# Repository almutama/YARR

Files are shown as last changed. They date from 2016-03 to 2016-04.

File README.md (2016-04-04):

#YARR (Yet Another RepRap)

YARR is an open source 3D printer designed and developed by LEDs & Chips Creative Electronics in Lisbon, Portugal. YARR is based on the [CoreXY](http://corexy.com/) technique and adds several improvements to other printers.  YARR is available either as a made to order kit or fully assembled from [Leds & Chips](www.ledsandchips.com)

##Technical specifications

###Dimensions
Custom-Sized
Built Version 7575
- Printer Dimensions: 1250(X) x 1250(Y) x 1250 mm(Z without bowden tupe support)
- Print Area Dimensions: 750(X) x 750(Y) x 750 mm(Z)
Built Version 5050
- Printer Dimensions: 1000(X) x 1000(Y) x 1000 mm(Z without bowden tupe support)
- Print Area Dimensions: 500(X) x 500(Y) x 500 mm(Z)

###Mechanical Construction
- OpenBuilds V-Slot aluminium frame
- OpenBuilds Wheels carriages X, Y, Z
- 4 motors Z Axis
- Flexible aluminium coupling for threaded rods of Z Axis
- 9 point print base levelling system with cushioning
- Quick change system for multi tools head
- Brushless Fans with axial ball bearings.

###Print resolution
- Very high: 60 microns
- High 100 microns
- Medium 200 microns
- Low 300 microns

###Extruder Mechanics
Custom extruder design
- 0.4mm nozzle
- Heat-sinks with axial fan
- Part cooling nozzle
Print speed
- Recommended speed: 70 mm / s
- Maximum recommended speed: 200 mm / s

###Electronics
- Any RepRap electronics conforming to RepRap Interface Standard RIS 1. Default: RAMPS 1.4
- LCD Panel with rotary encoder and push-button navigation for autonomous printing
- Cold glass base (size:750 x 750 x 4 mm)
- Power supply: 220 AC 12 DC 100W
- Thermistor 100k EPCOS
- Heating element: 12V 40W

###Software
- Firmware derivative Marlin
- Recommended environment: Cura Software
- Supported Files:. Gcode
- OS supported:
	- Windows XP and above
	- Mac OS X and above
	- Linux

###Communications
- Standard SD card reader
- USB Port Type B

###Materials
- PLA Filament 1.75-mm

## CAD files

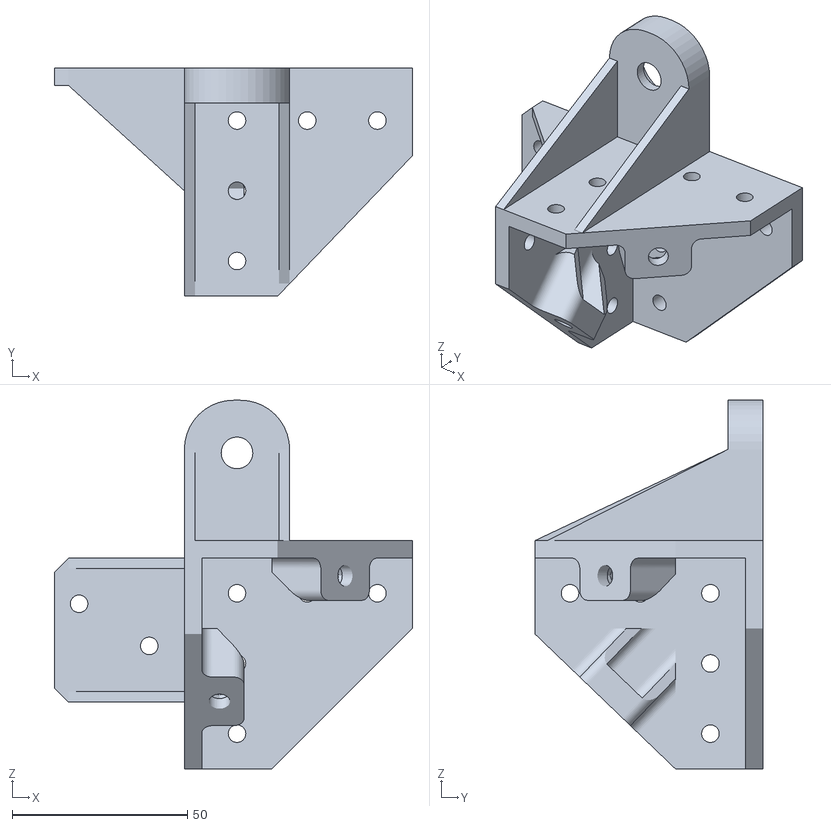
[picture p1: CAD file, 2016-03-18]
cad_models/STL/stl 01/roll support xy 02.STL
102.0 x 65.0 x 105.0

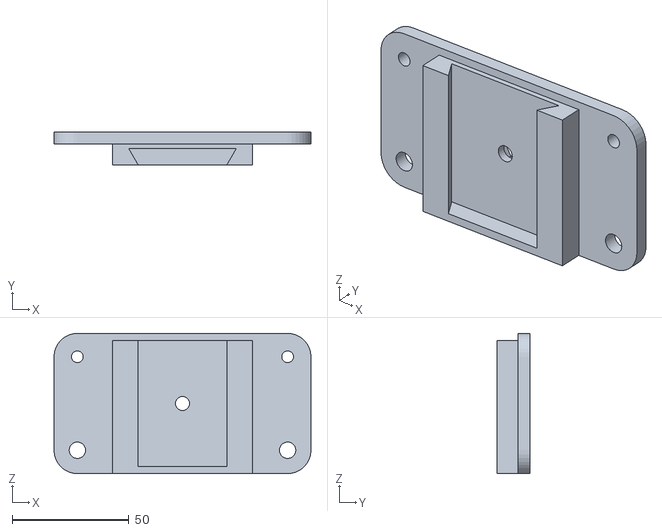
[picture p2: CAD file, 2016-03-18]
cad_models/STL/stl 02/slider plate y 02.STL
110.0 x 14.0 x 60.0

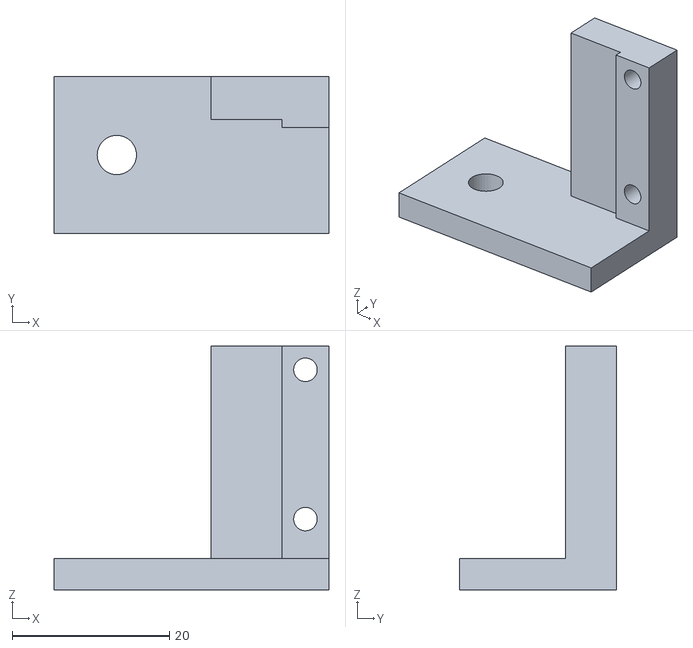
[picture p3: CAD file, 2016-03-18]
cad_models/STL/stl 03/endstop holder.STL
35.0 x 20.0 x 31.0

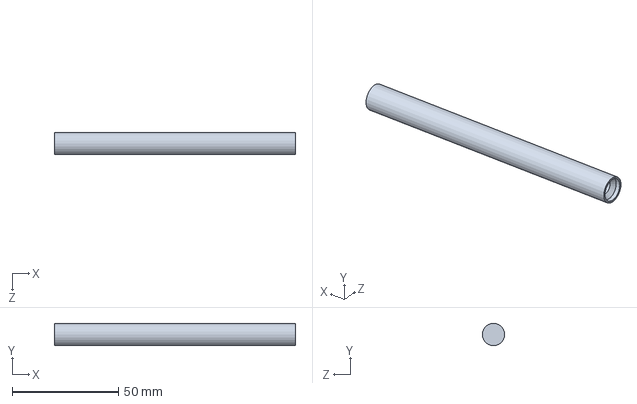
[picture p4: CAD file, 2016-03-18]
cad_models/STL/stl 04/knife body 01.SLDPRT
113.3 x 10.5 x 10.5 mm

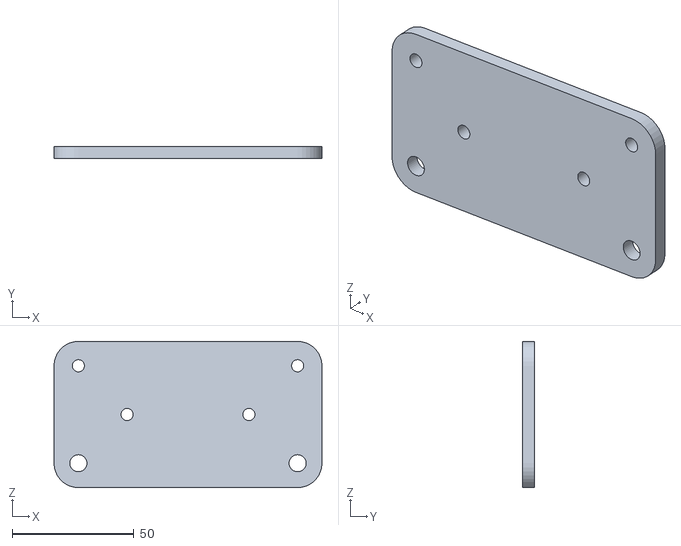
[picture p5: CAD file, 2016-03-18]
cad_models/STL/stl 05/slider plate y 01.STL
110.0 x 5.00 x 60.0

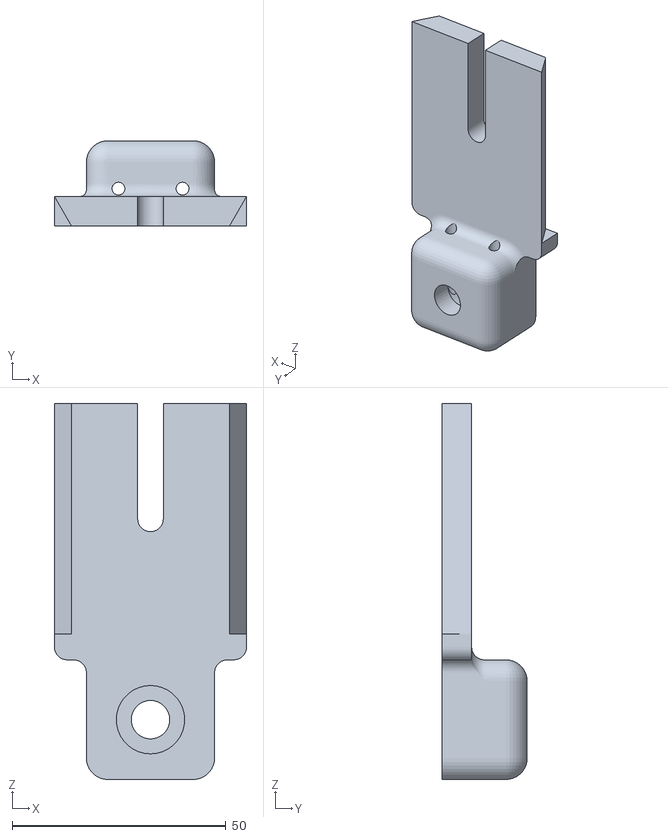
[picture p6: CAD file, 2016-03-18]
cad_models/STL/stl 06/extruder bowden 175 support 01.STL
45.0 x 20.0 x 88.0

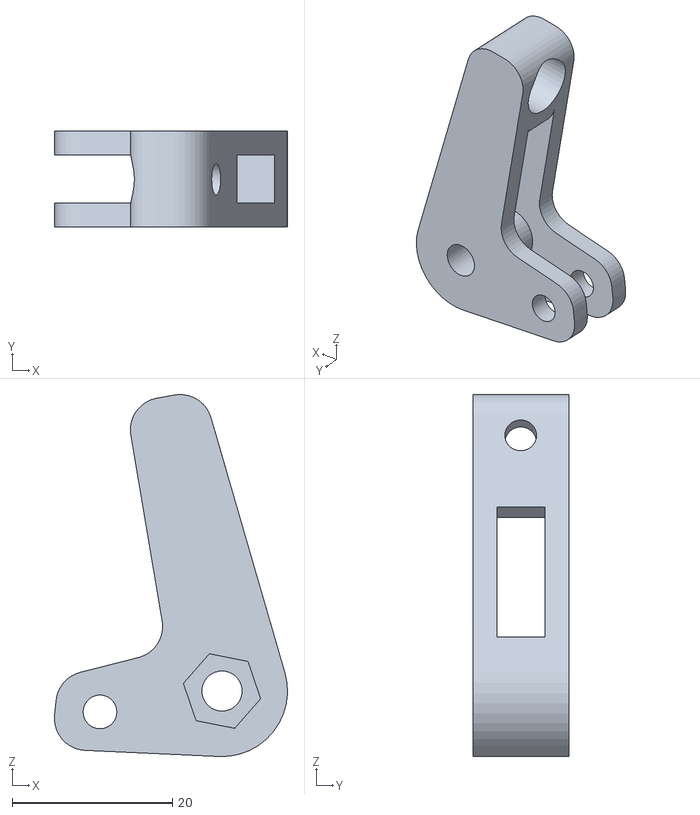
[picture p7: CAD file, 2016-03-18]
cad_models/STL/stl 07/extruder filament pusher 02.STL
29.0 x 12.0 x 45.1

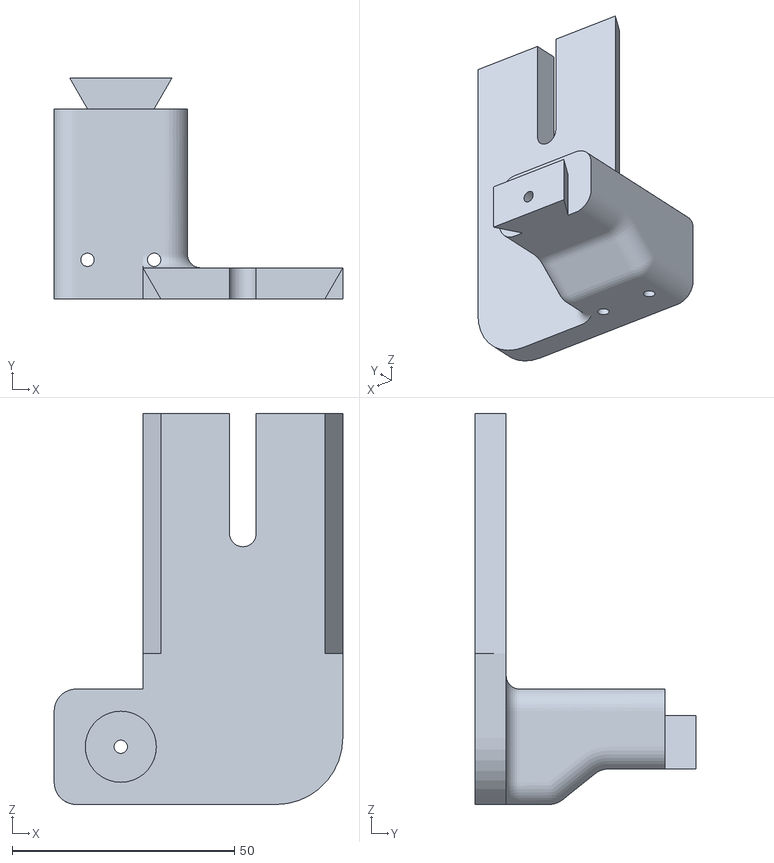
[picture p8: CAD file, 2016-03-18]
cad_models/STL/stl 08/extruder mini bowden support 01.STL
65.0 x 49.7 x 88.0

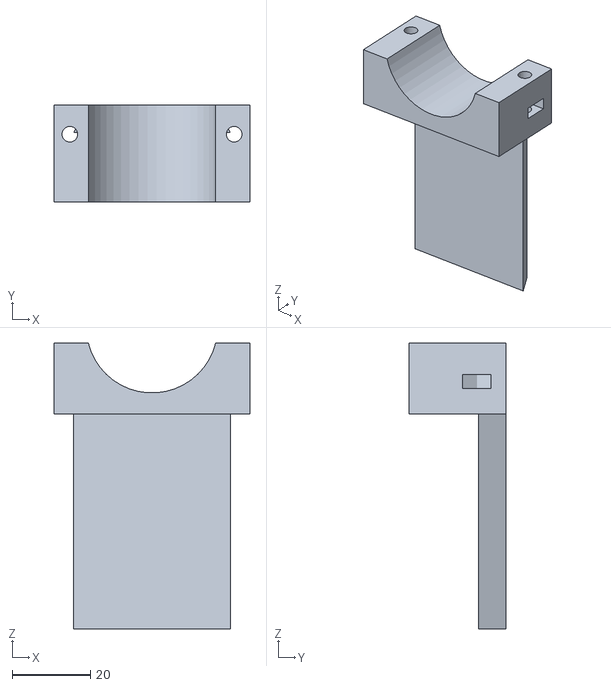
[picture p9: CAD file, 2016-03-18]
cad_models/STL/stl 09/mill adapter 01 01.STL
50.0 x 24.9 x 73.1

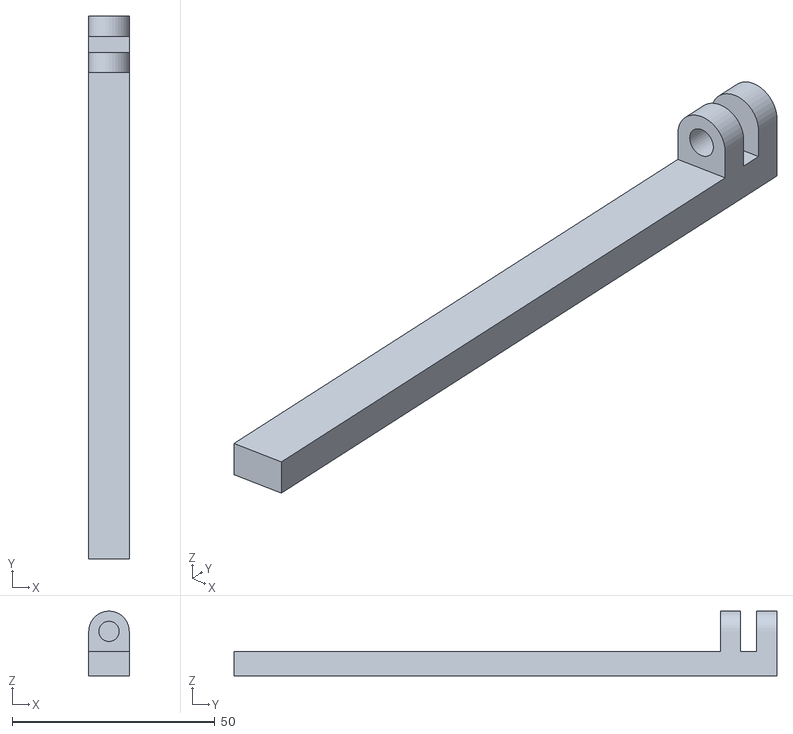
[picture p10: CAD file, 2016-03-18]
cad_models/STL/stl 10/endstop ruler 01.STL
10.00 x 134.0 x 16.0

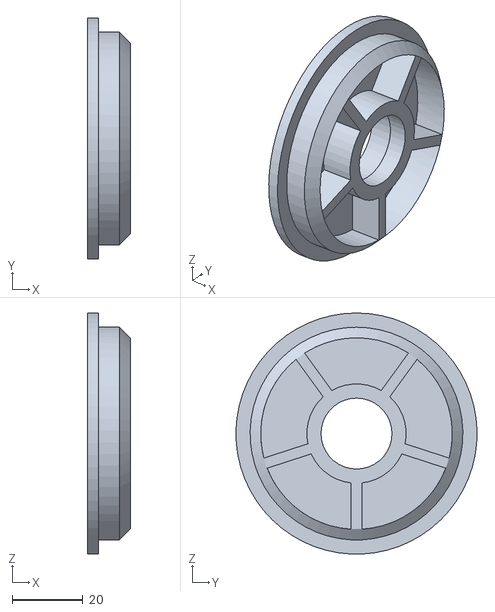
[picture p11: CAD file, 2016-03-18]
cad_models/STL/stl 11/spool holder bearing insert 04.STL
12.0 x 68.0 x 68.0

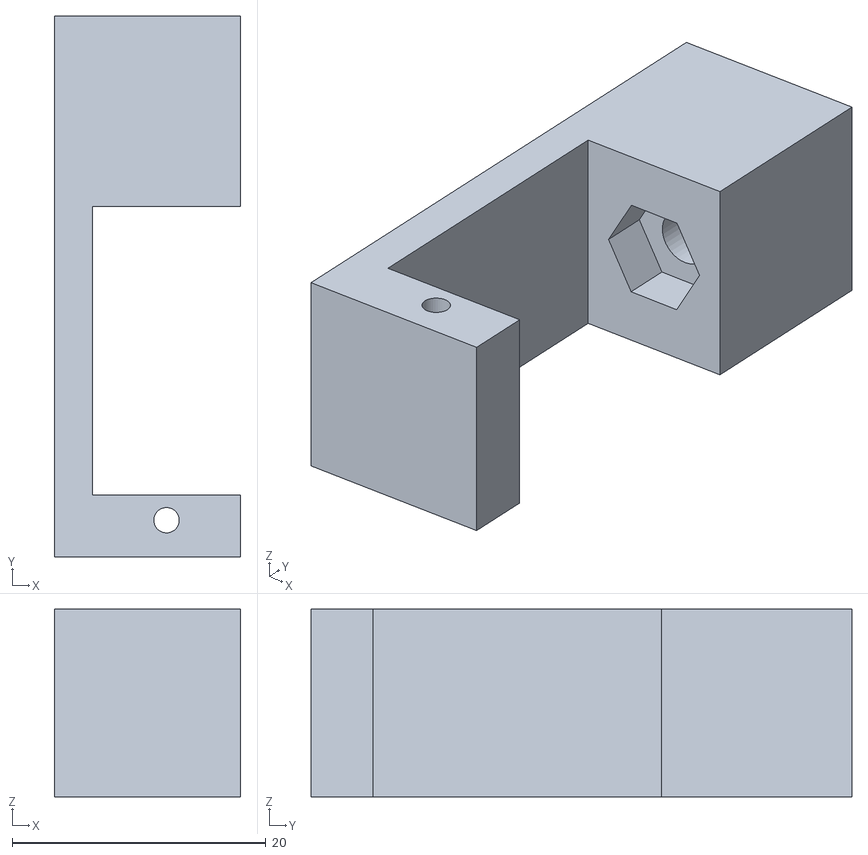
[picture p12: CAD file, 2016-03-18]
cad_models/STL/stl 12/suport servo.STL
14.7 x 42.6 x 14.8

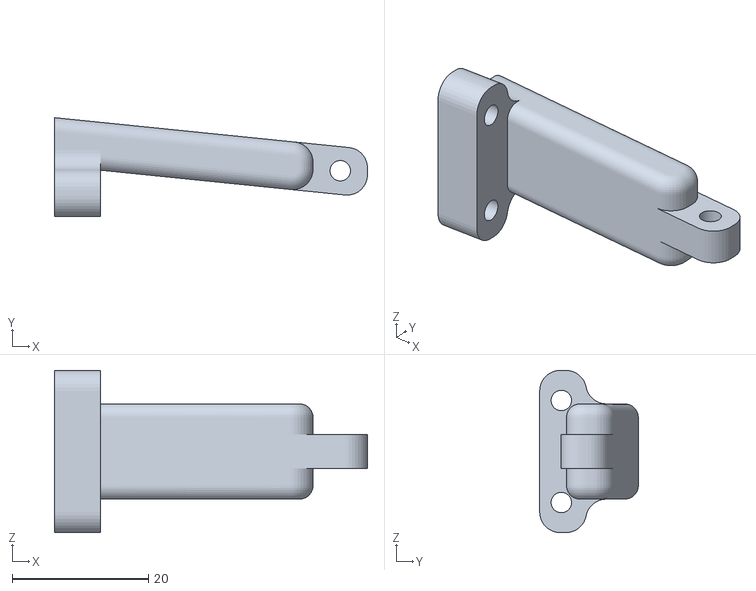
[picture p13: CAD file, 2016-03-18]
cad_models/STL/stl 13/fan support direct drive 01.STL
46.0 x 14.5 x 23.8

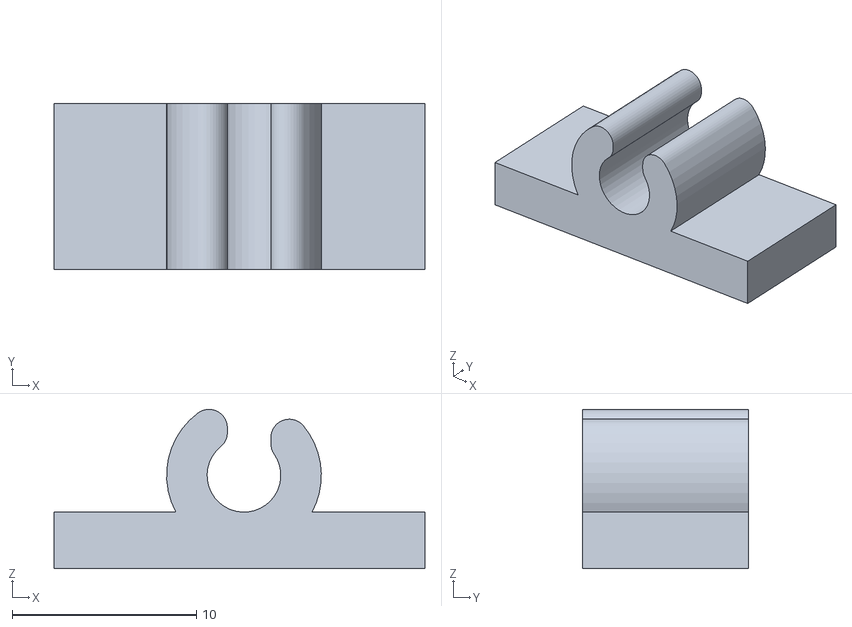
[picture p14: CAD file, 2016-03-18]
cad_models/STL/stl 14/dobradiça fémia.STL
20.1 x 9.00 x 8.64

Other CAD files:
cad_models/STL/stl 15/cutting adapter 02.STL
cad_models/STL/stl 16/slider x plate 01.STL
cad_models/STL/stl 01/slider plate z 02.STL
cad_models/STL/stl 02/slider x plate 01.STL
cad_models/STL/stl 01/roll support xy 01.STL
cad_models/STL/stl 03/cable hider 01.STL
cad_models/STL/stl 03/cable hider 02.STL
cad_models/STL/stl 03/cable hider 03.STL
cad_models/STL/stl 03/endstop holder 01.STL
cad_models/STL/stl 04/glass support angle.STL
cad_models/STL/stl 04/glass support handle.STL
cad_models/STL/stl 04/glass support straight.STL
cad_models/STL/stl 04/knife holder.STL
cad_models/STL/stl 05/slider plate x greg extruder.STL
cad_models/STL/stl 06/bolt hobber bearing.STL
cad_models/STL/stl 06/extruder filament pusher 02.STL
cad_models/STL/stl 07/extruder bearing adapter 01.STL
cad_models/STL/stl 07/extruder filament pusher 03.STL
cad_models/STL/stl 07/extruder motor support 01.STL
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

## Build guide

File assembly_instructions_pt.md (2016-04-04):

##Passo 1
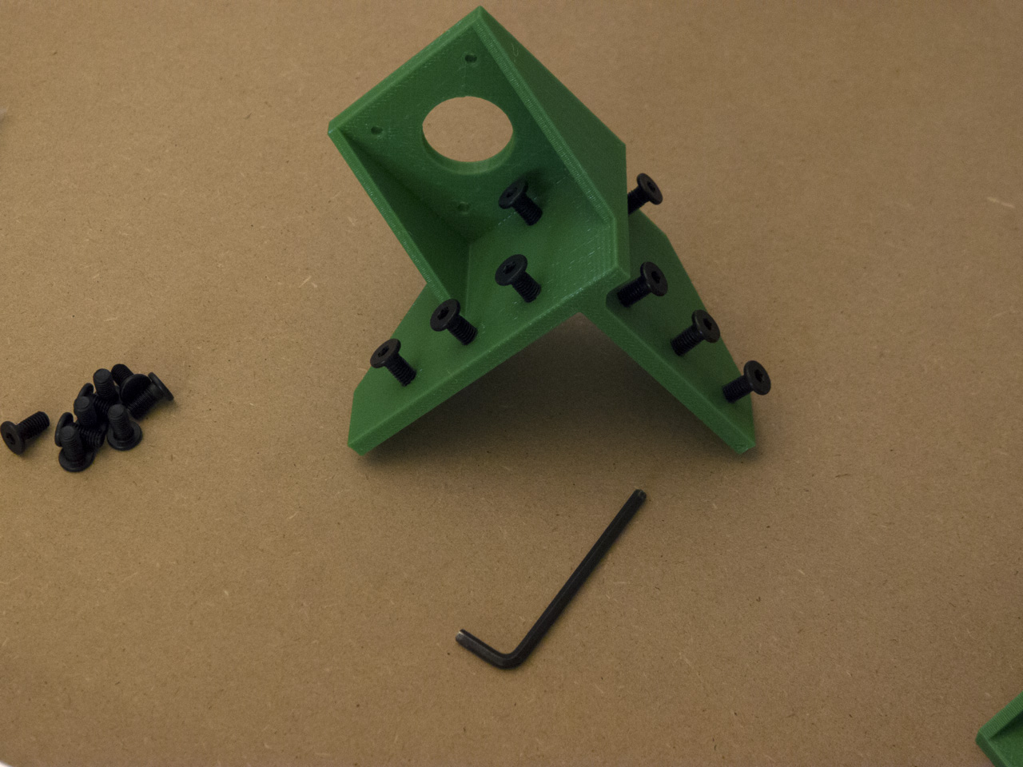
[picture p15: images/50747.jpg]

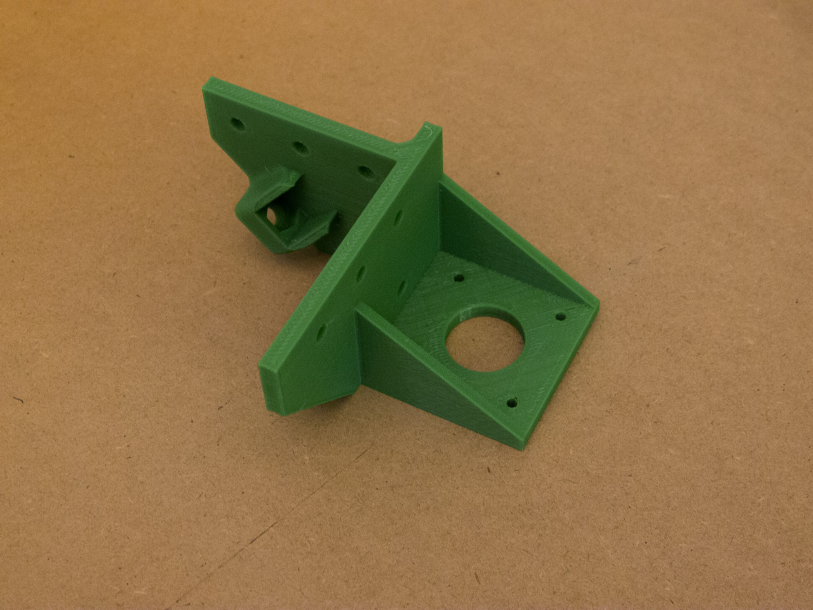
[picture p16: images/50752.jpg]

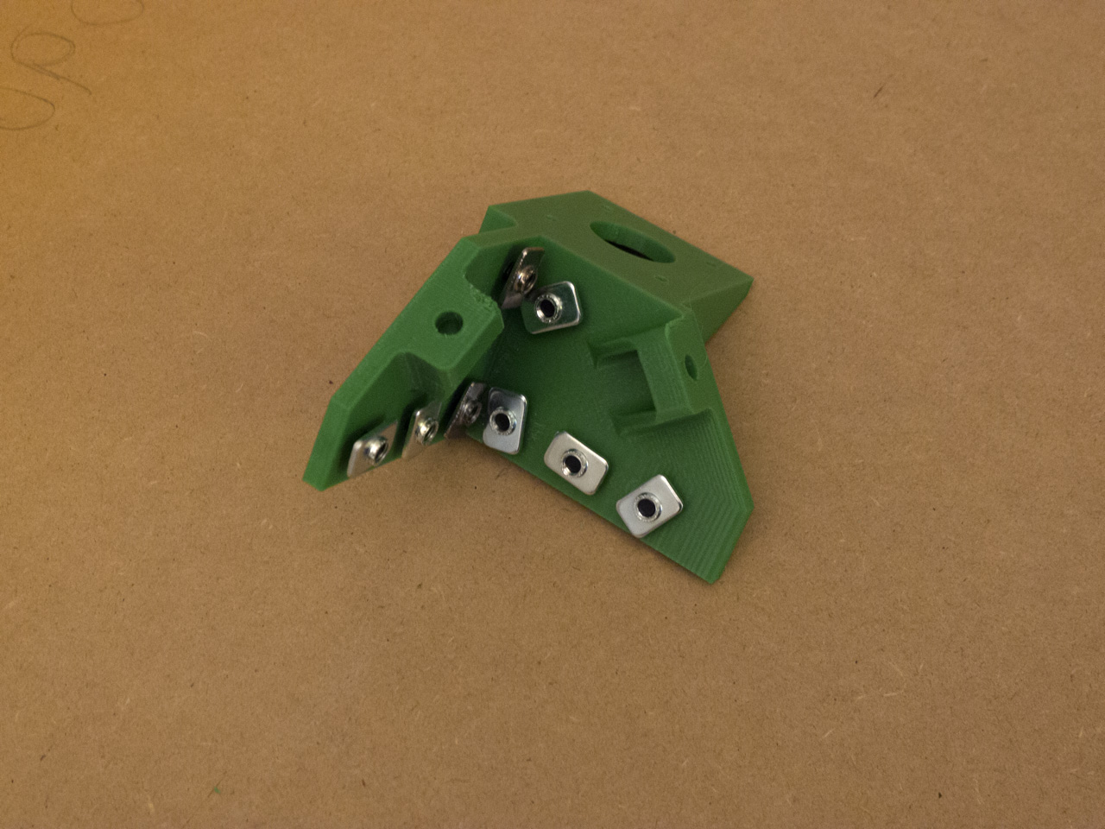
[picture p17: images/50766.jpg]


Coloque 8 parafusos M5-10mm como descrito na figura bem como as respectivos Tee Nuts.
Repita este procedimento para as outras 3 peças.  

##Passo 2
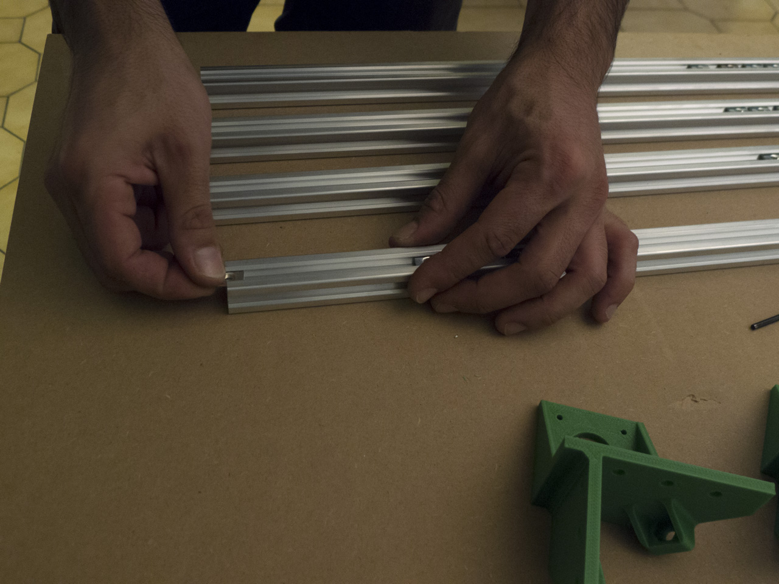
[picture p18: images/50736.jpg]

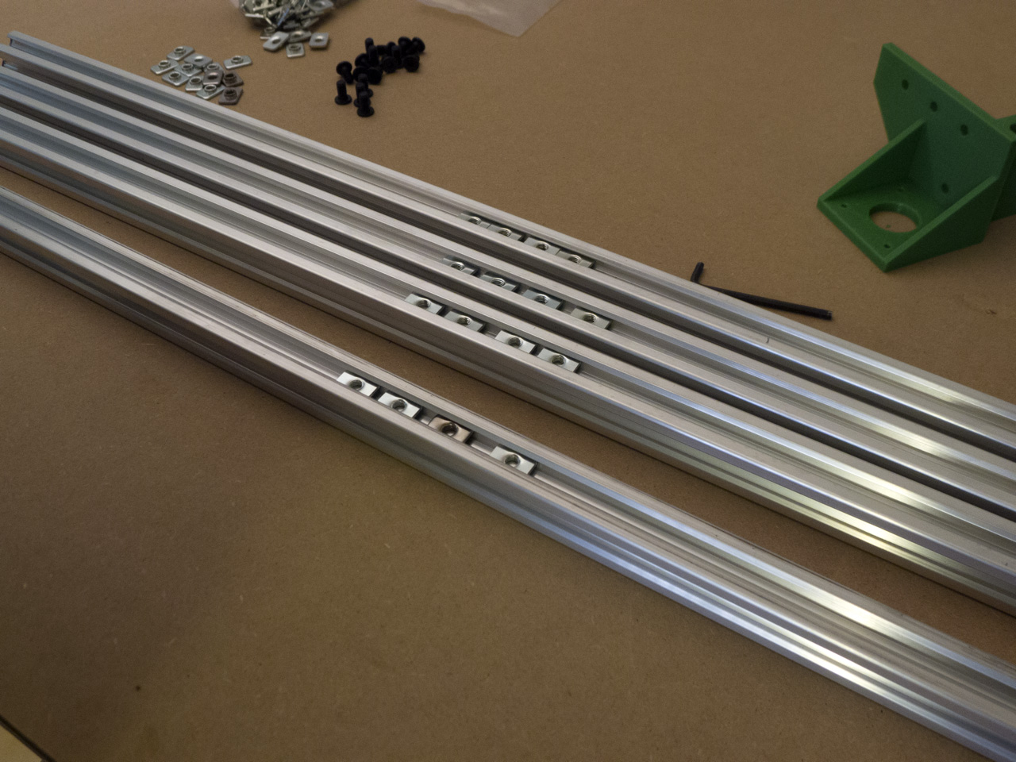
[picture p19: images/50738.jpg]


Introduza 4 tee nuts num perfil de aluminium, tenha em atenção pois a parte saliente de cada Tee nut tem que ficar para o lado de dentro do perfil.
Repita este procedimento mais 3 vezes.
Este 4 perfis farão a base da máquina e estes 4 Tee Nuts, por varão vão servir para fixar a impressora á plataforma de madeira, que servirá de base.
 
##Passo 3
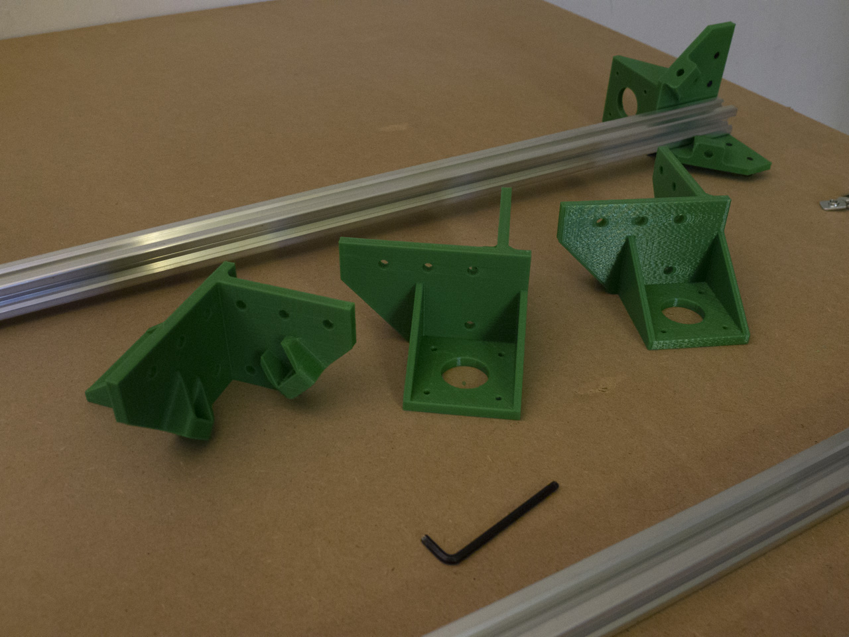
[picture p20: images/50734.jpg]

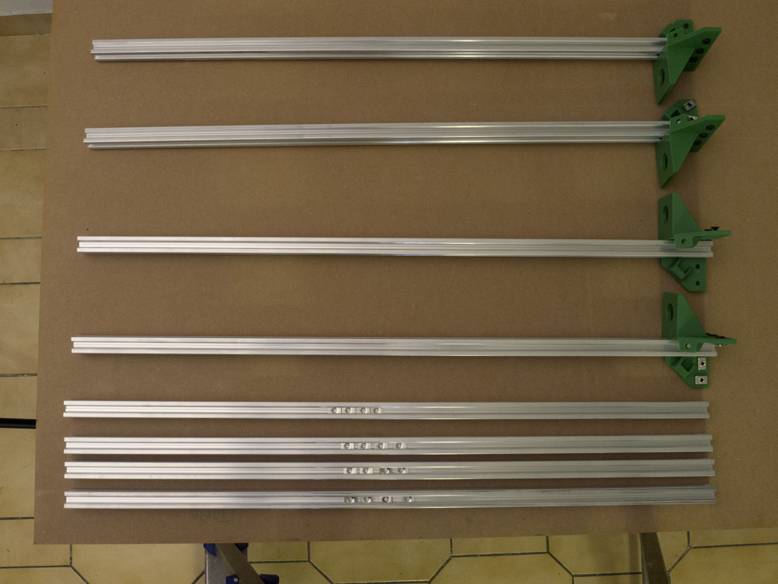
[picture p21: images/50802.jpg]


Encaixe um perfil de aluminium ao alto, em cada peça previamente preparada no passo 1, tal como se apresenta na figura ao lado.

##Passo 4
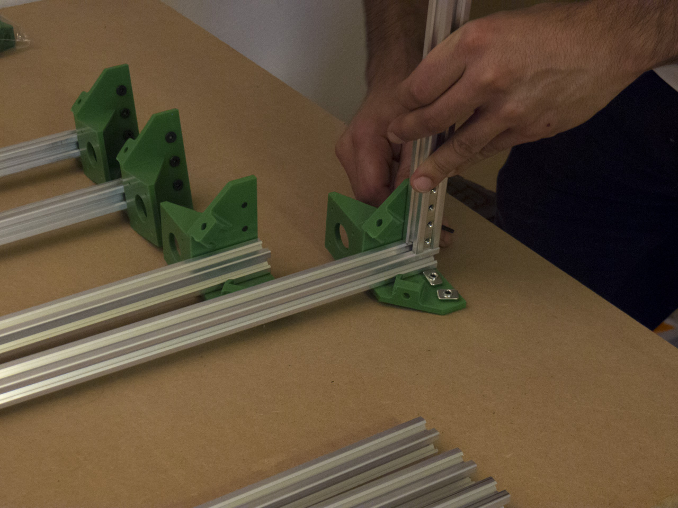
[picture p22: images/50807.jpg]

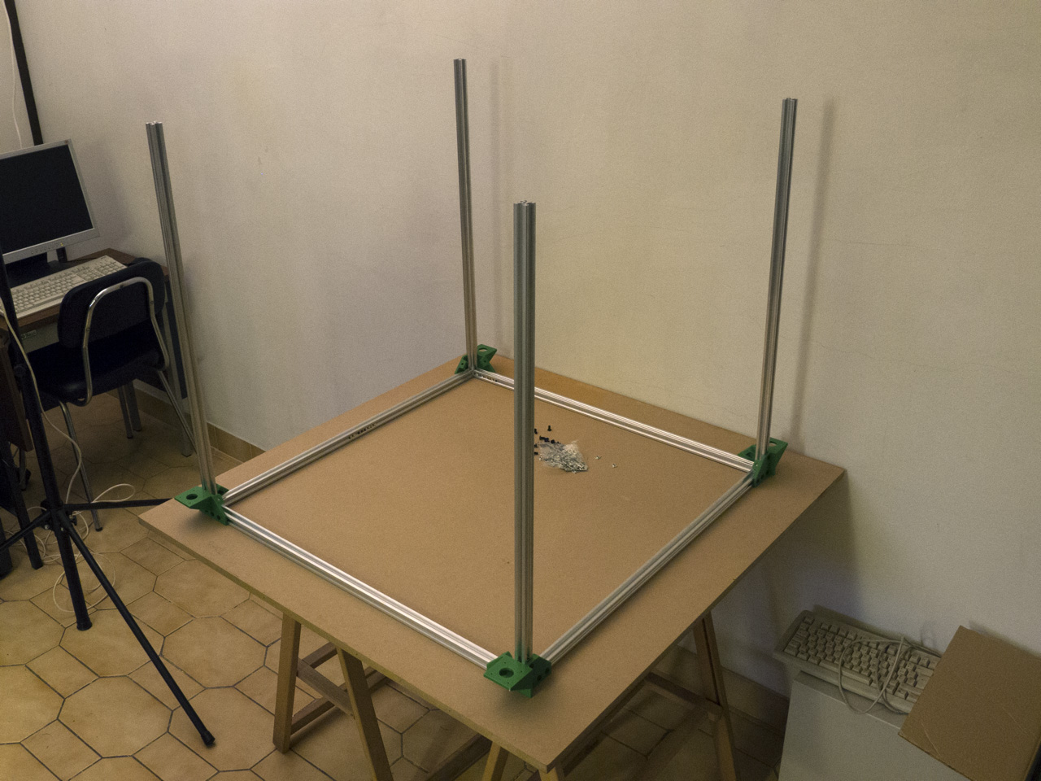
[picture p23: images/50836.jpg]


Coloque os varões, previamente preparados no passo 2, assegurando que os 4Tee nuts ficam virados para o lado de dentro da máquina.
É importante que a peças impressas fiquem com a disposição como se apresentam na figura.

##Passo 5
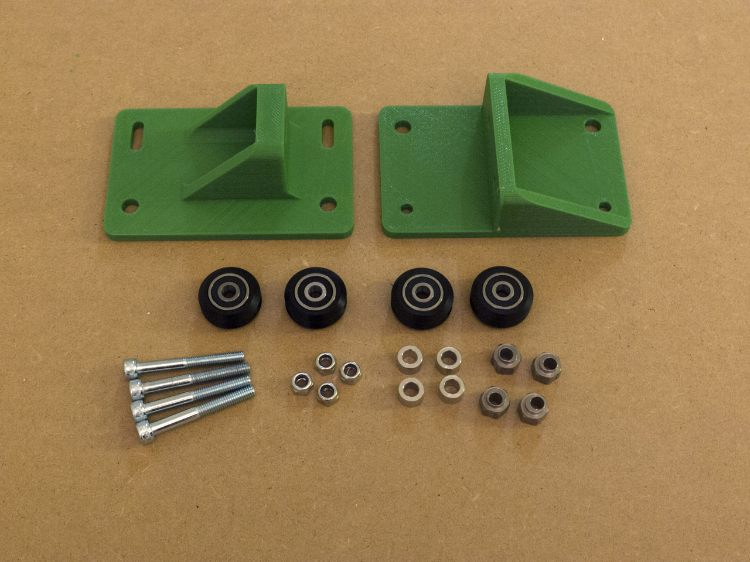
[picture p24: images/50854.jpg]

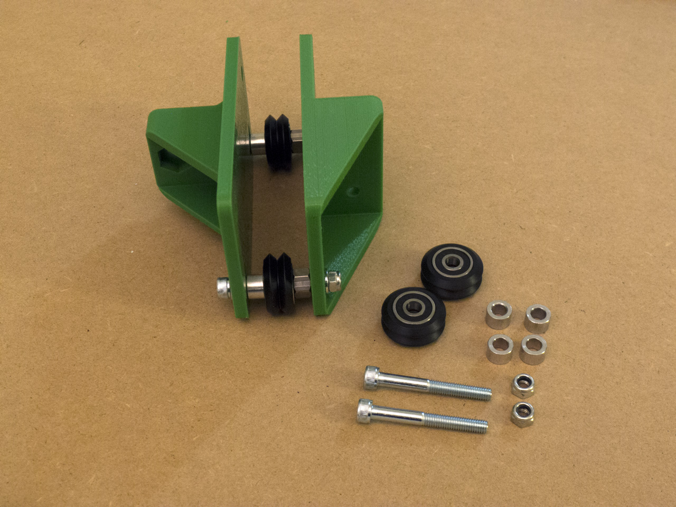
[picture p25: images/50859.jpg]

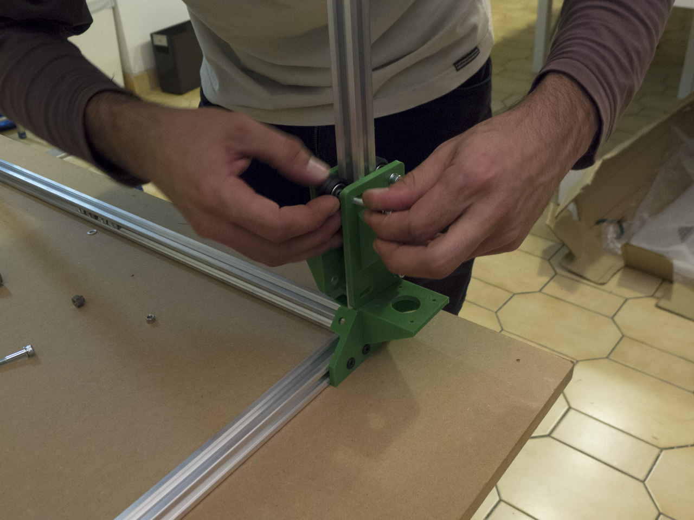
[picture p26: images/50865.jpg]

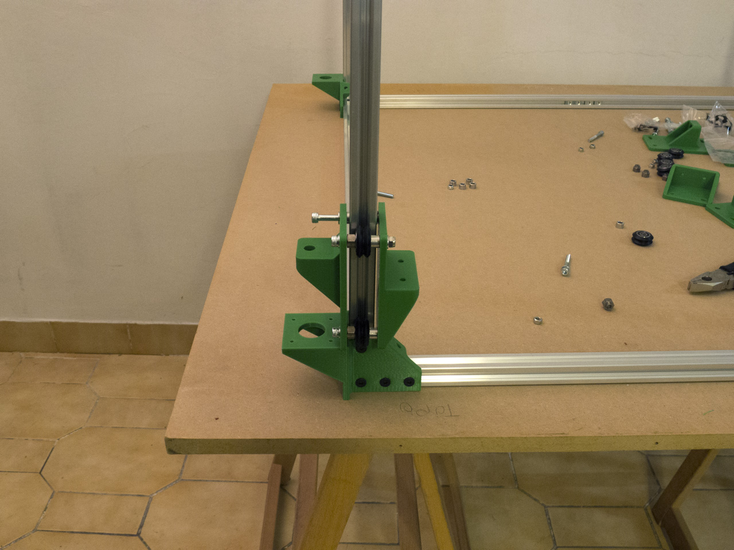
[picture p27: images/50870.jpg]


Efetue a montagem do carril do eixo Z como descrita na imagem.
repita este passo 3 vezes.
Introduza um carril em cada perfis que se encontra na vertical.
Tenha em atenção que os espaçadores excêntricos tem que está rodados de forma a que as rodas não façam força no perfil de aluminium.  
Após a sua instalação a tensão nas rodas deve ser ajustada
rodando os excêntricos até sentir que as rodas ficam á justa e não rodam só por si. 

##Passo 6
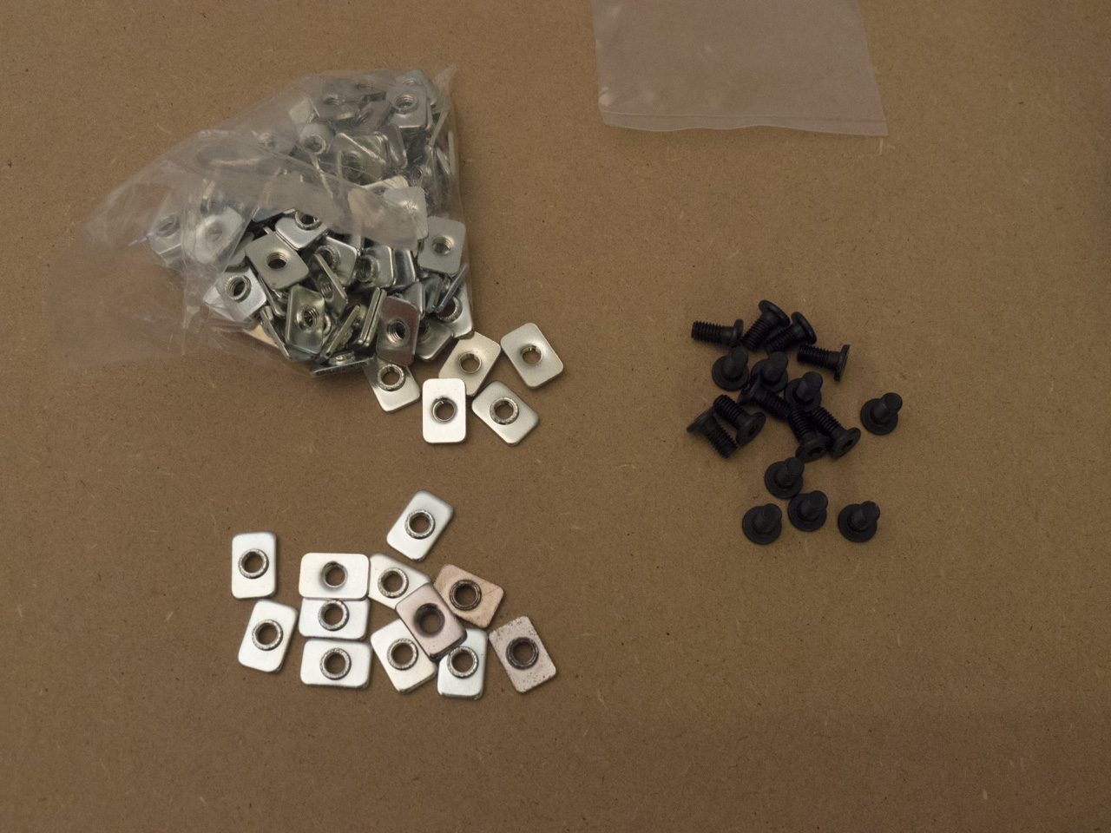
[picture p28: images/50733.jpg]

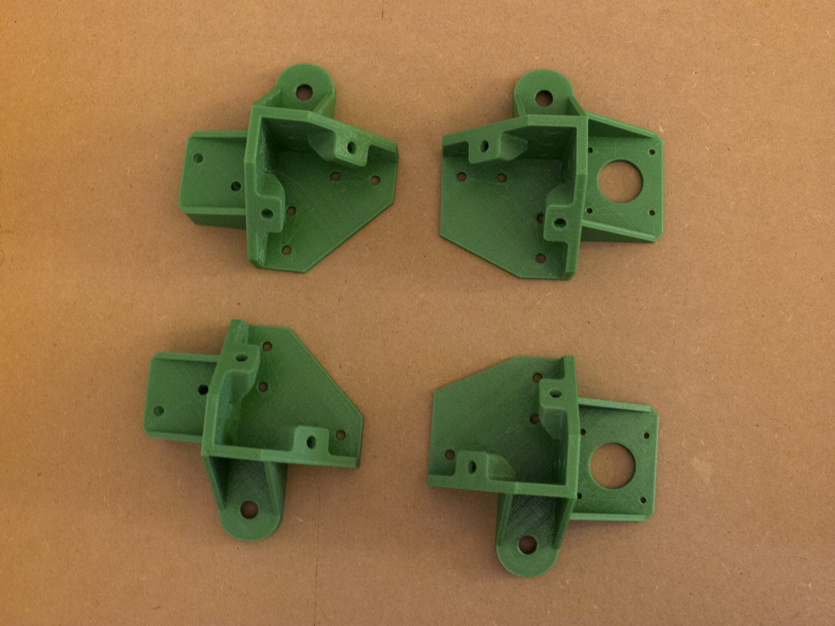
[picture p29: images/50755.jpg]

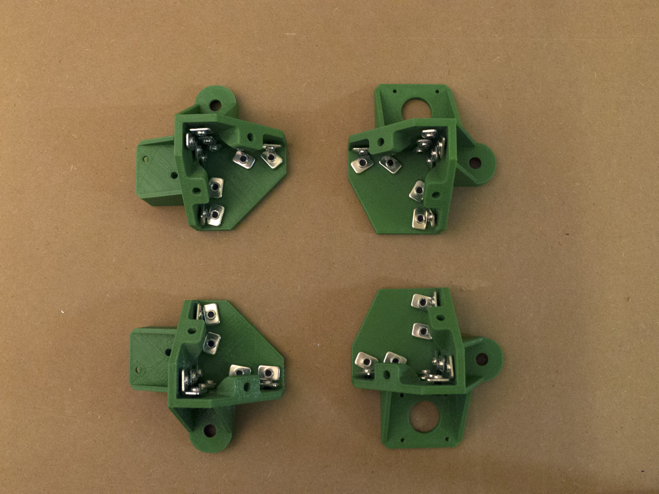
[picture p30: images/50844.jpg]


Coloque 8 parafusos M5-10mm como descrito na figura bem como as respectivos Tee Nuts.
Repita este procedimento para as outras 3 peças.  

##Passo 7
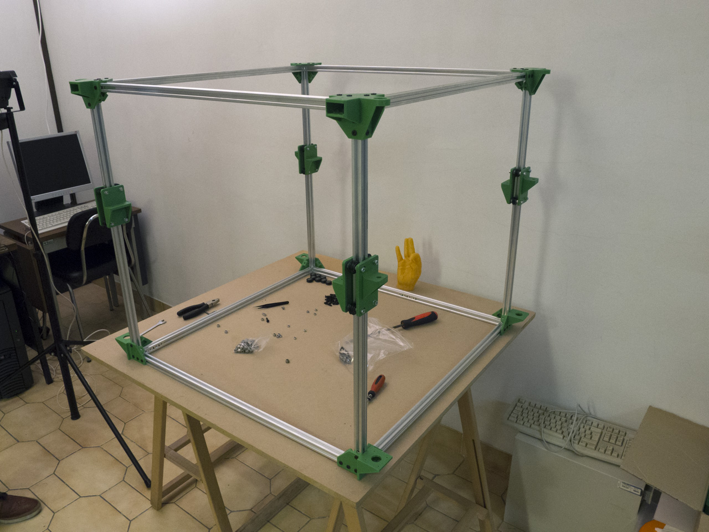
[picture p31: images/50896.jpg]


Neste passo vamos colocar 4 perfis de aluminium juntamente com as peças preparadas no passo anterior fazendo assim um “Moldura” e por sua vez colocamos essa moldura no topo da estrutura.
Mais uma vez é importante ter em conta a orientação das partes impressas.
A frente da nossa impressora vai ser o lado onde, na figura, se encontra a mão amarela.

##Passo 8
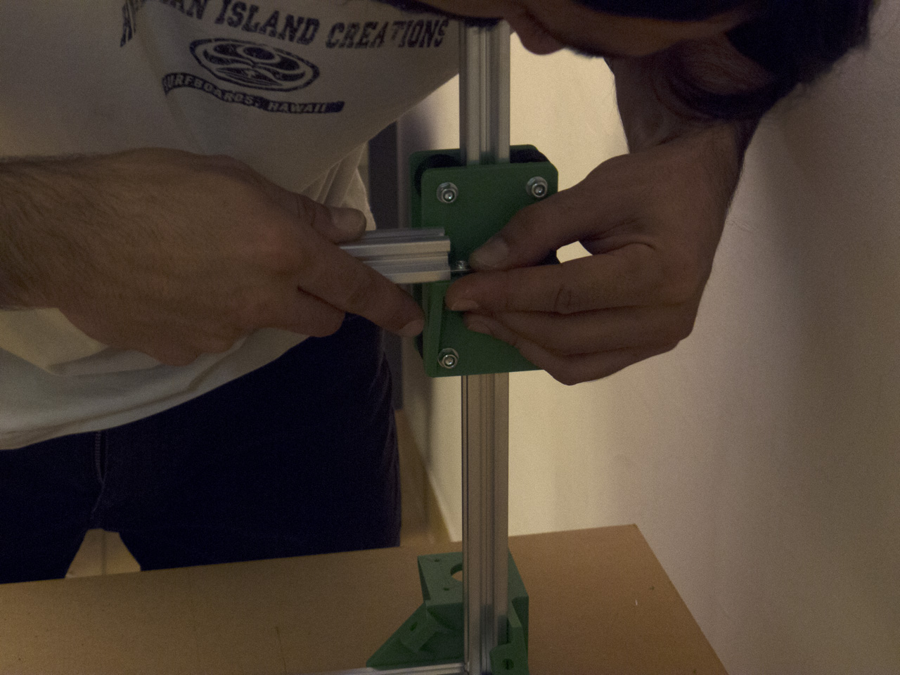
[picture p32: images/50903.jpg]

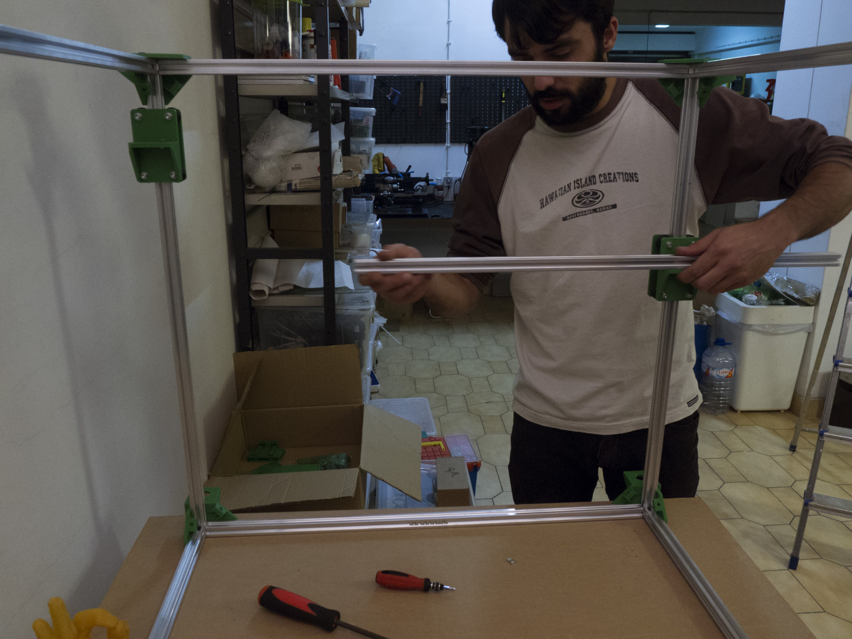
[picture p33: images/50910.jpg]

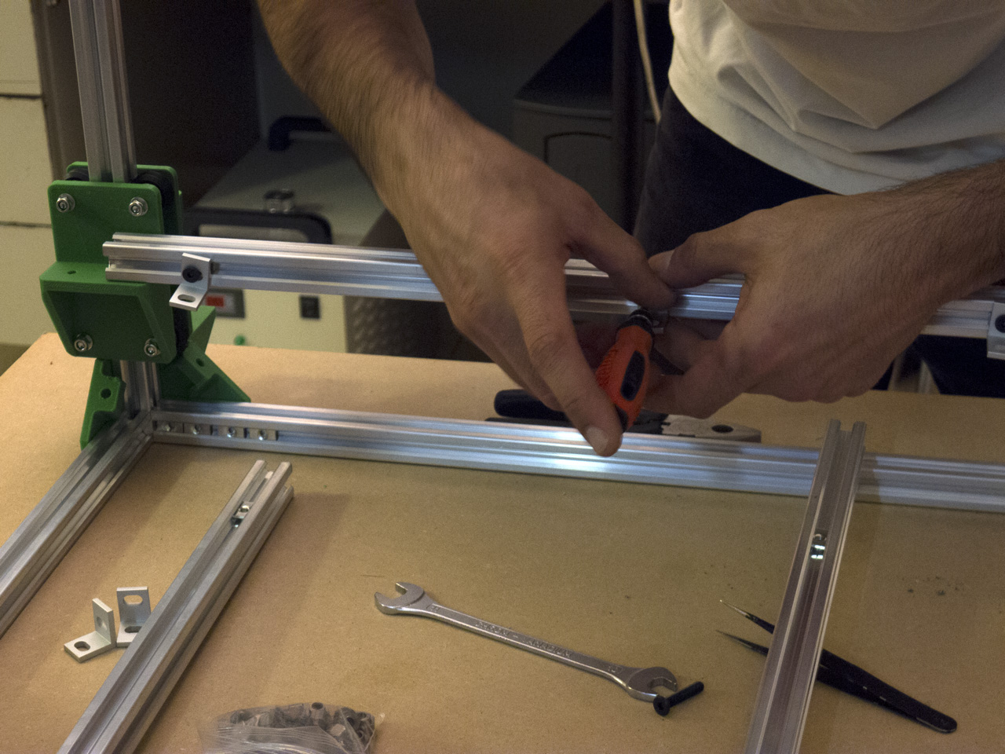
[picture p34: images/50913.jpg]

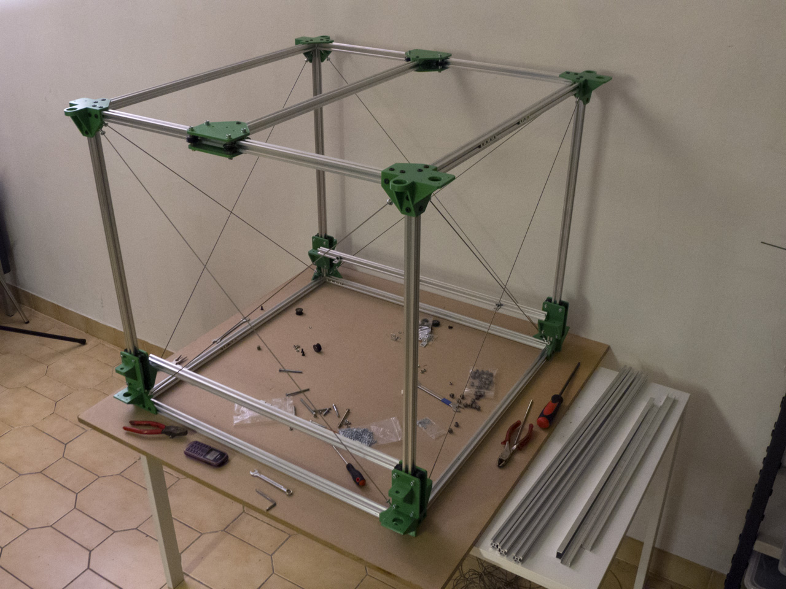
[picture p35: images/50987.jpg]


Introduza um parafuso M5 10mm juntamente com um teenut em cada um dos carris de z. em seguida introduza um perfil de aluminium  de um carri de z para o outro ( é importante que esses dois perfiz fiquem nas laterais da máquina).
Em seguida introduza 3 tee nuts em cada um dos perfis bem. em cada um desses tee nuts introduza um parafuso a fim de fixar um angulo de aluminium como se apresenta na figura.

##Passo 9
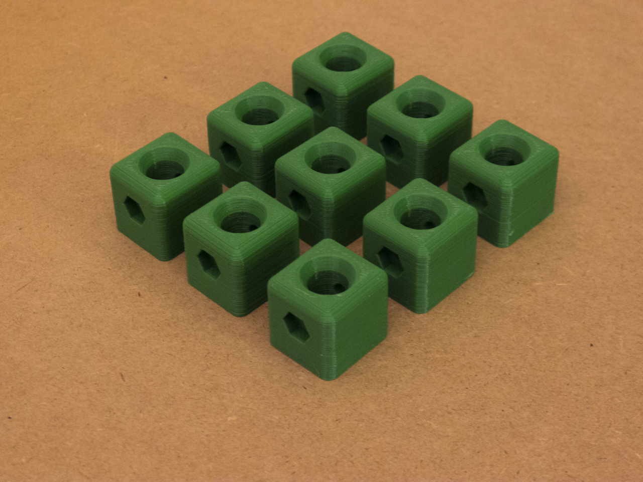
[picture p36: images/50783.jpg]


Sobre os dois perfis colocados previamente no carril de z, coloque 3 perfis de aluminium que vão ser fixados na parte de baixo dos “ângulos” de aluminium previamente colocados.
É importante que estes perfis fiquem mais ou menos equidistantes.
Em seguida coloque 3 tee nuts por perfil e uma peças quandradas como se apresenta na figura ao lado fixada em cada tee nut.
Mais uma vez é importante que as peças fiquem mais o menos equidistantes.   

##Passo 10
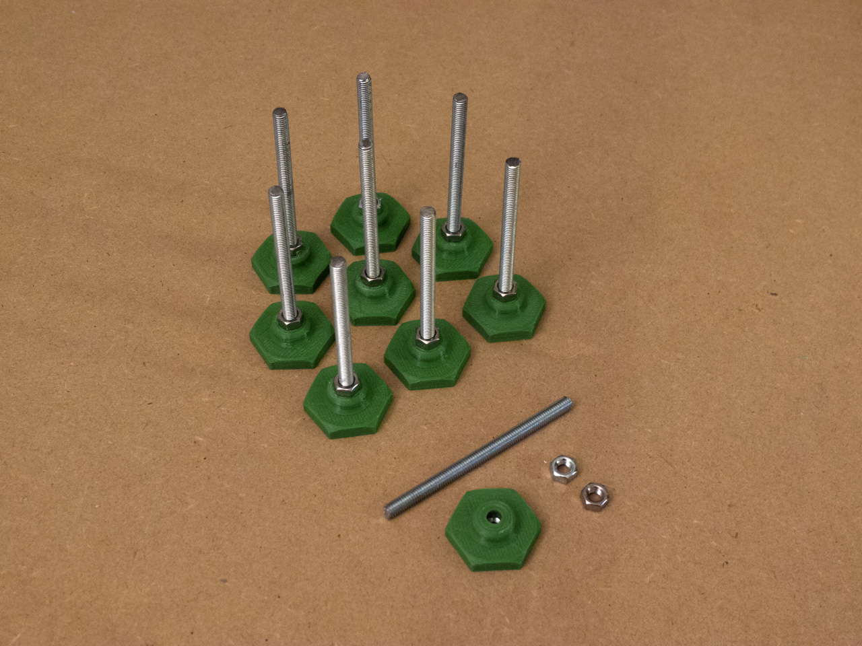
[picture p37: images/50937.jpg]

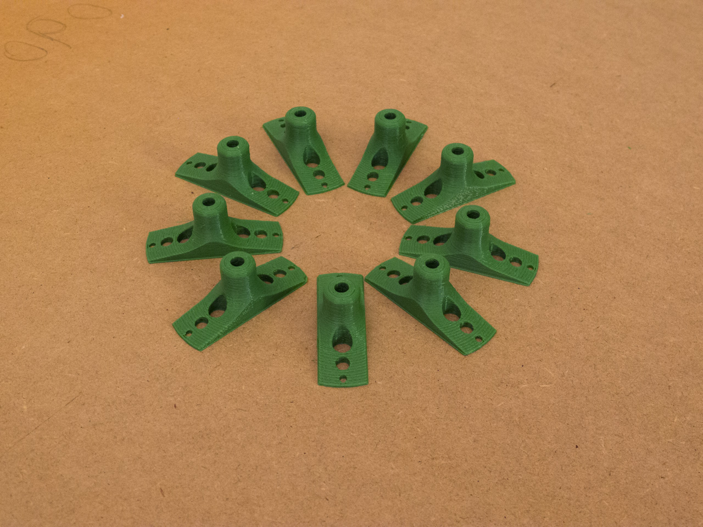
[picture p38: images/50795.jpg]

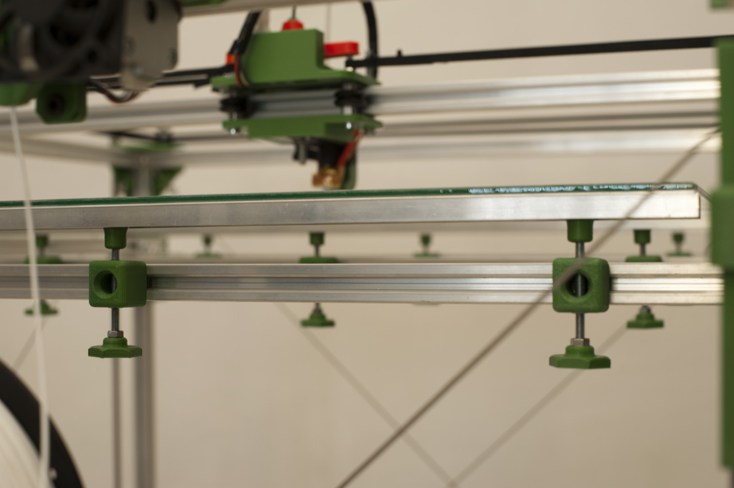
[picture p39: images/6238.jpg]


Introduza duas porcas M5 ( uma em cima outra em baixo)  em cada uma das peças quadradas previamente fixadas nos prefis. 
Em seguida rosque uma manipulo de reguração de altura em cada uma das estruturas previamente montadas (peça quadrada fixada no perfil e com duas porcas M5).
Em seguida no topo de cada varão coloque um pé
Coloque um perfil em U na horizontal sobre os “pés” sendo que cada perfil vais estar sobre 3 desse pès. 

##Passo 11
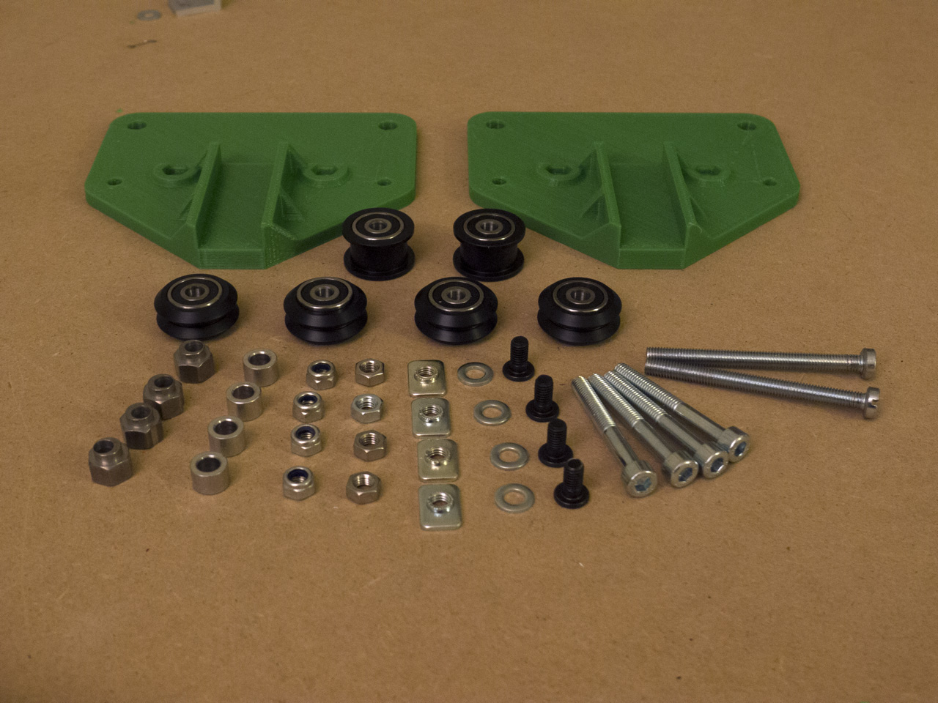
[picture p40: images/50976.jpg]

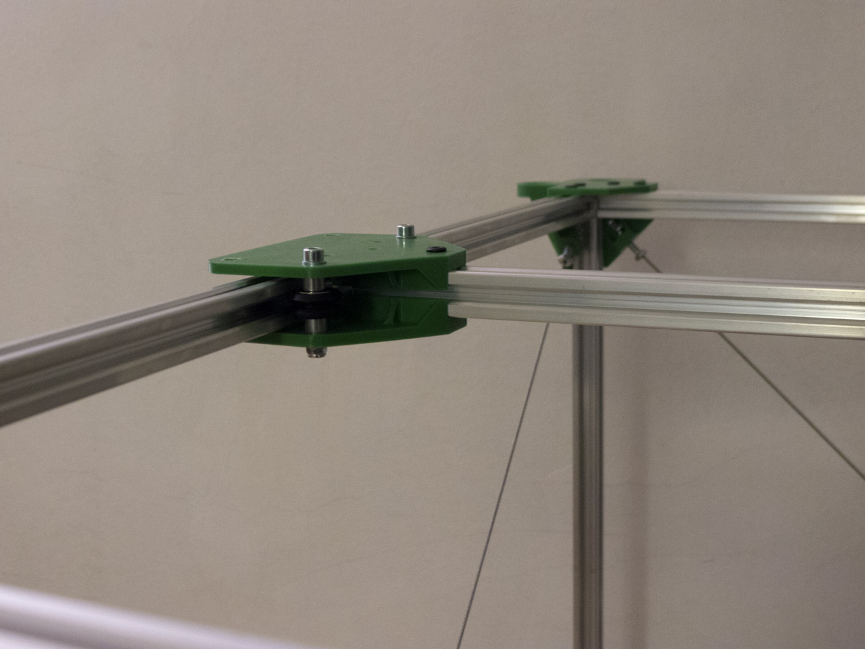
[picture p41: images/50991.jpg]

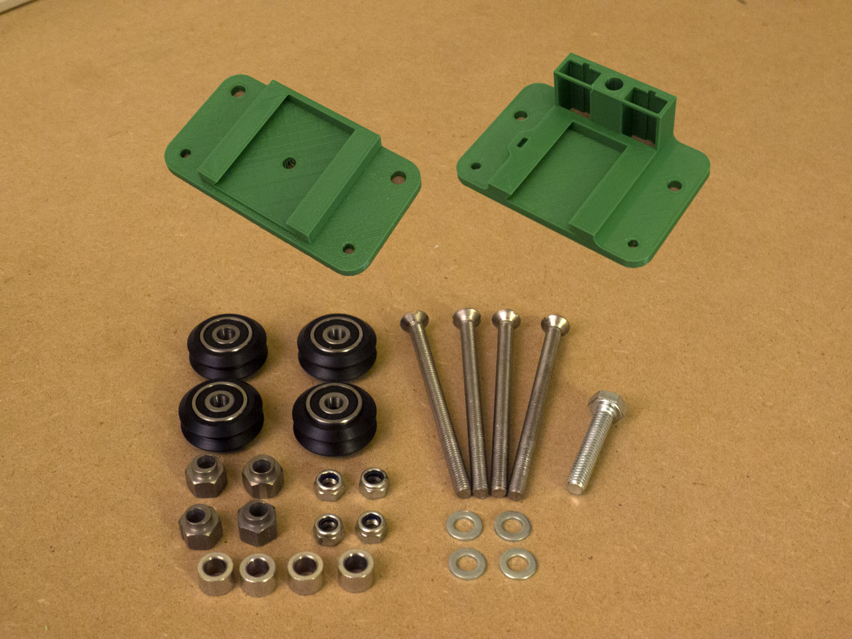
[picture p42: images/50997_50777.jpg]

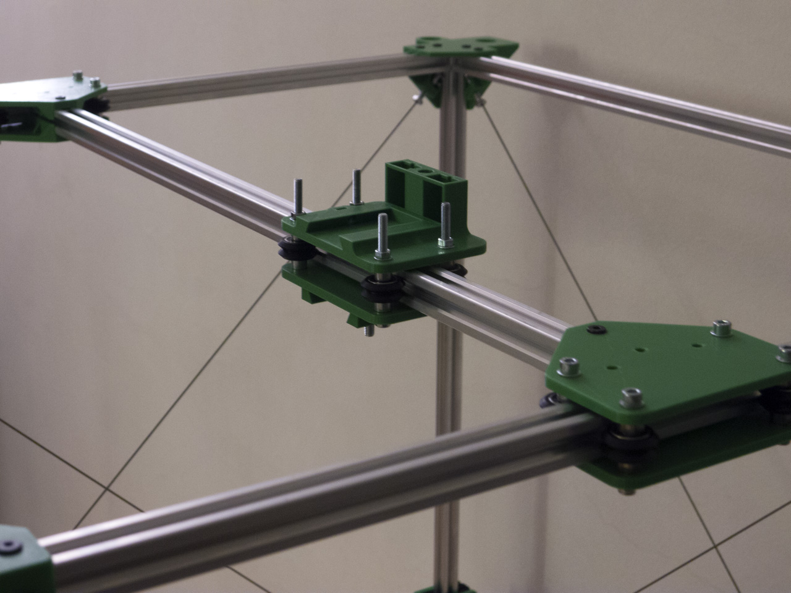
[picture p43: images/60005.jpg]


Introduza o carri de X num perfil de aluminium e em seguida coloque em cada extremidade do perfil uma carruagem de Y como na figura.
É importante respeitar a disposição dos carris.
no caso de ter os carris pré montado retire dos carris de Y as duas rodas que ficam orientadas par fora, a fim de introduzir a estrutura na montagem já efectuada.

##Passo 12
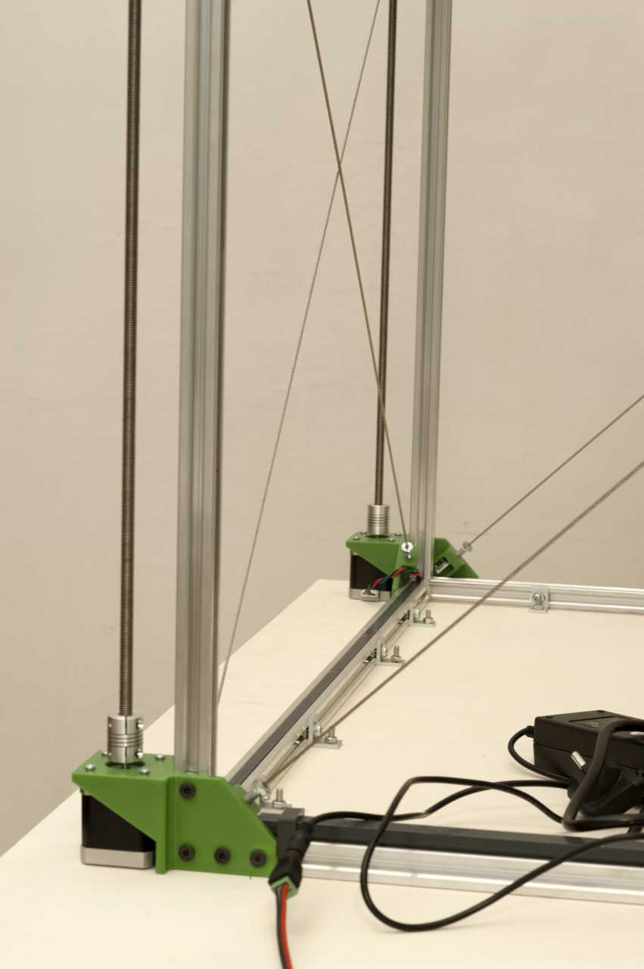
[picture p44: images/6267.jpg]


Instale os 4 motores de Z nas peças impressas como de acordo com a figura bem como os acopladores.
Em seguida coloque uma porca M8 em cada um dos carris de Z.  
Em seguida rosque o varão de cima para baixo passando pela porca e fixando no acoplador.
Para trancar o varão coloque duas porcas no topo do varão e aperte uma contra a outra.

##Passo13
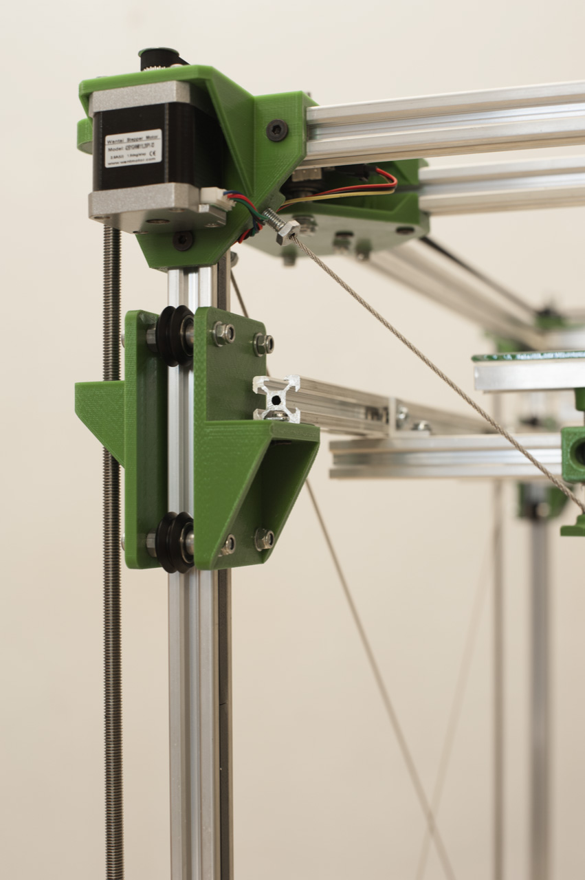
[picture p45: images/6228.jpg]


Introduza os motores ( X Y ) na peças impressas que se encontram nos cantos superiores da montagem bem como um pulley em cada motor.

##Passo14
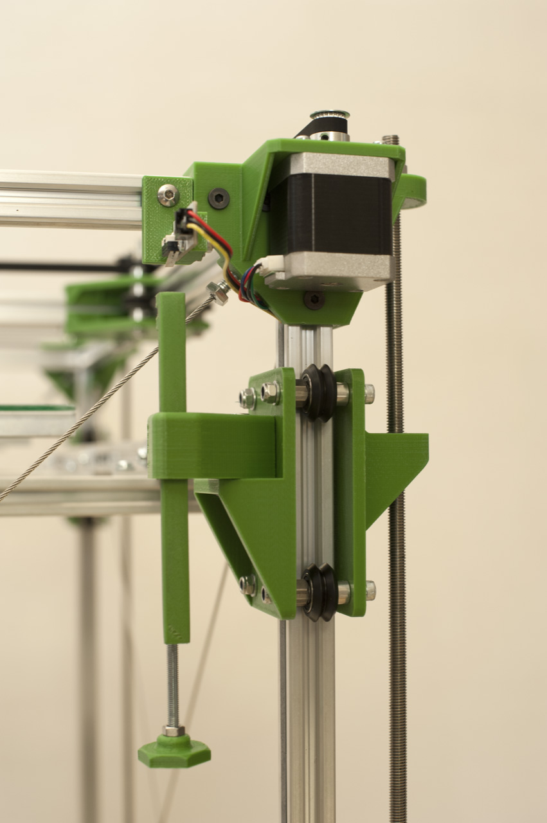
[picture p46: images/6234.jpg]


Olhando de frente para a máquina, introduza a montagem do fim de curso, no carril de z de acordo com a figura.

##Passo 15
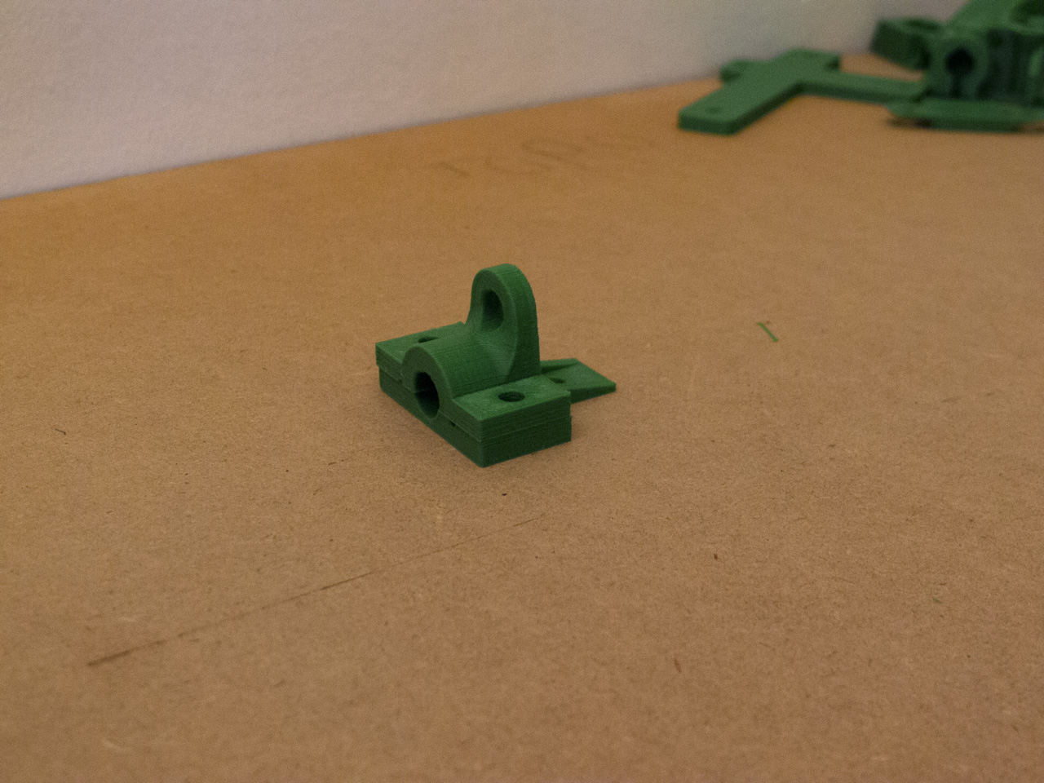
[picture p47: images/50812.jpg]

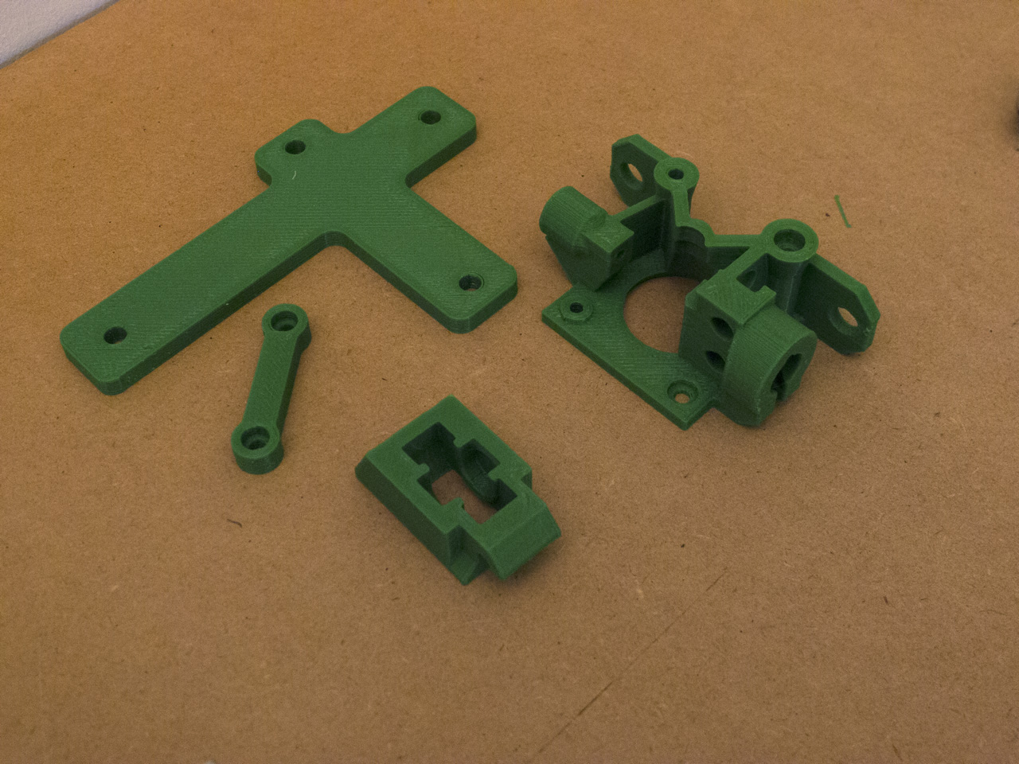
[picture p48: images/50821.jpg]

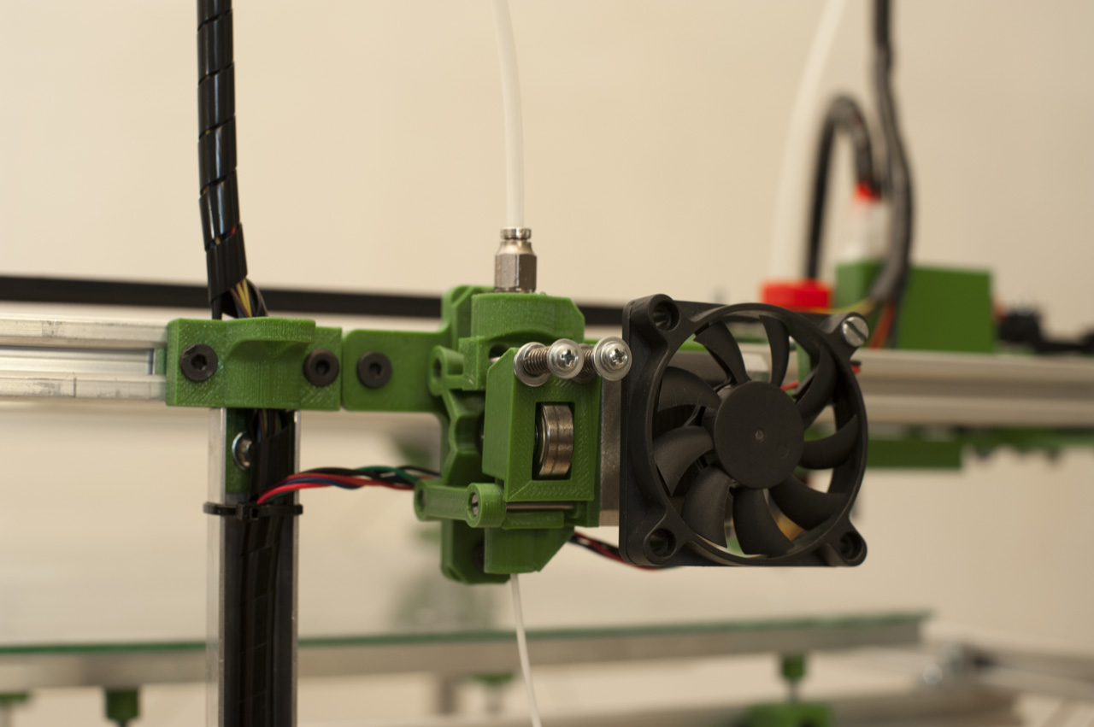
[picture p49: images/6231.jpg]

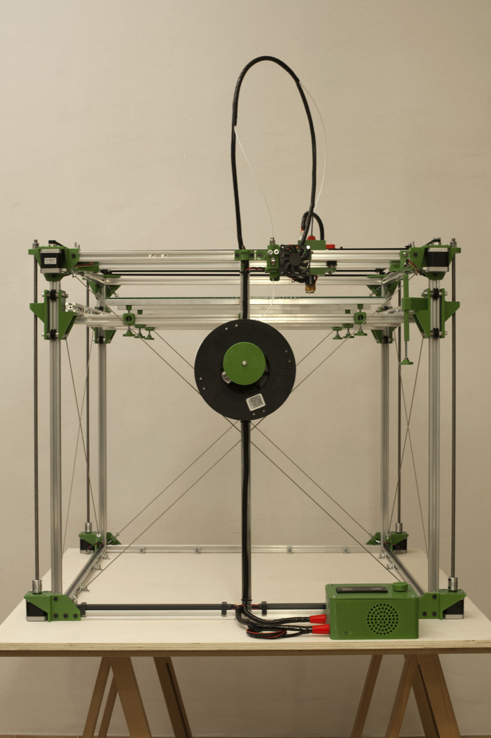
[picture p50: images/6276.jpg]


Olhando de frente para a máquina.
No perfil de aluminium superior introduza 4 Tee Nuts e no perfil inferior 1 Tee Nut. 
Instale a montagem do fixador do guida de cabos, no centro do perfil de aluminium superior. Logo ao lado direito instale a montagem do extrusor de acordo com a figura.
Em seguida fixe o perfil que vai guiar os cabos no perfil inferior.
É importânte respeitar sempre a orientação das montagen em relação á imagem.  

##Passo 16
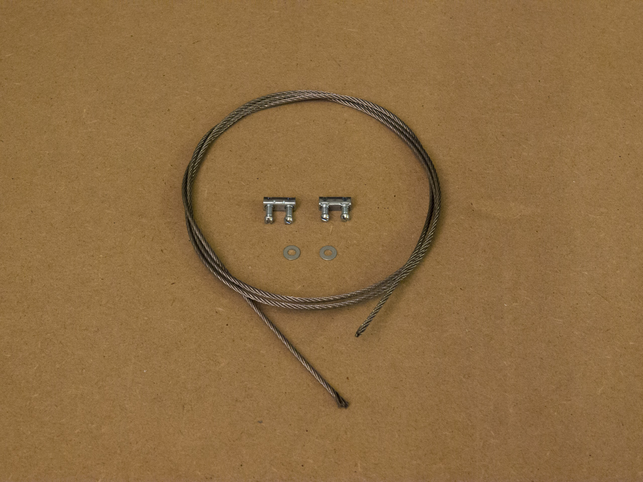
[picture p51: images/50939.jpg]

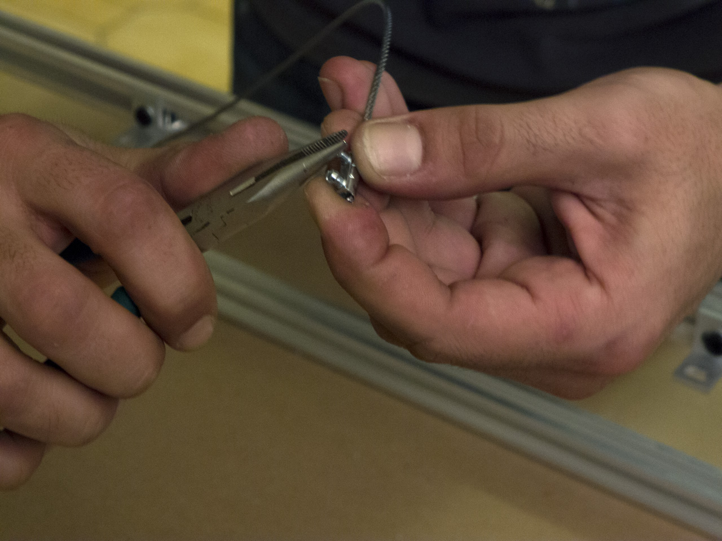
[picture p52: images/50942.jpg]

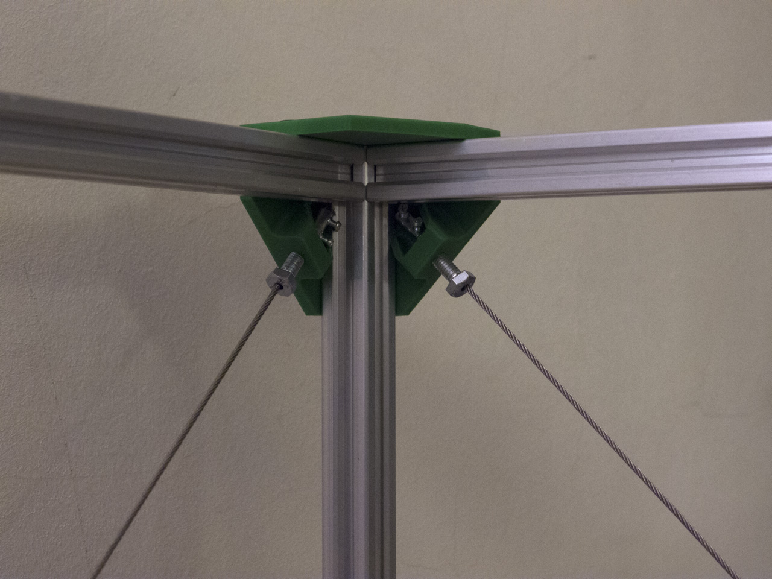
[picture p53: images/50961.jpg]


Neste passo é muito importante fazer o corte do cabo de aço de forma a que não fique desfiado pois isso felicitará os seguintes passos. 
Corte o cabo de aço em 8 partes iguais, de comprimento igual a diagonal da máquina.
Em cada um dos cantos impressos tem 2 parafuso fixos por uma porca. Desaperte todos os parafusos de forma a ficarem o mais para fora possivel mas fixos á porca.

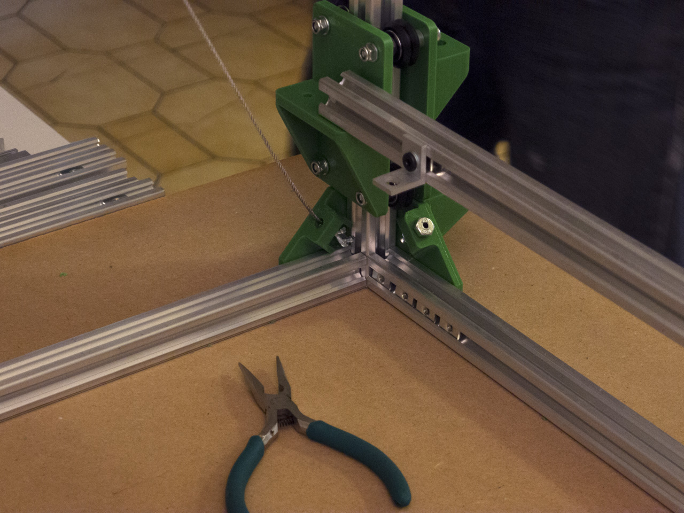
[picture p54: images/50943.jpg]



Introduza uma peça de fixação na extremidade de um cabo de aço e uma anilha, aperte os 2 parafusos. 
Em seguida passe o cabo por um dos parafusos que encontra já instalado num dos cantos impressos e passe também pelo parafusos do canto oposto ficando o cabo na diagonal.
Introduza uma anilha na ponta do cabo de aço e de seguida uma peça de fixação, estique o cabo e com o cabo em tensão aperte os 2 parafusos do fixador.
Repita estes passos para as outras 7 diagonais da máquina.
Por fim aperte os parafusos por onde o cabo passou até estarem em tesão.



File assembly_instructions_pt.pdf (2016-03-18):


Coloque 8 parafusos M5-10mm como descrito na figura bem como descrito na figura bem
como as respectivos Tee Nuts.

Repita este procedimento para as outras

3 peças.

Passo 1


Introduza 4 tee nuts num perfil de aluminium, tenha em atenção pois a parte sa liente

de ca

da

Tee nut tem que ficar
para o lado de dentro do perfil.

Repita este procedimento mais 3 vezes.

Este 4 perfis farão a base da máquina e estes 4 Tee Nuts, por varão vão servir para fixar a impressora á plataforma de madeira que servirá de base madeira, que servirá de base.

Passo 2


Encaixe um perfil de aluminium ao alto, em ca a peça previamente prepara

da
no passo 1, tal como se apresenta na figura ao lado.

Passo 3



Coloque os varões, previamente preparados no passo 2,
asseguran o que os 4Tee nuts ficam virados para o lado de dentro da máquina.

mportante que a peças
impressas fiquem com a disposição como se apresentam na figura.

Passo 4


Efetue a montagem do carril do eixo Z como descrita na imagem. repita este passo 3 vezes.

Introduza um carril em cada perfis que se encontra na vertical.

Tenha em atenção que os
espaçadores excêntricos tem que está rodados de forma a que as rodas não façam força no perfil de aluminium.

Após a sua instalação a tensão nas rodas deve ser ajustada
rodando os excêntricos até sentir que as rodas ficam á justa e não rodam só por si.

Passo 5


Coloque 8 parafusos M5-10mm como descrito na figura bem como as respectivos Tee Nuts.

Repita este procedimento para as outras 3 peças.

Passo 6



Neste passo vamos colocar 4 perfis de aluminium juntamente com as peças preparadas no passo anterior fazendo assim um “Moldura” e por sua vez colocamos essa moldura no topo da estrutura.

Mais uma vez é importante ter em conta a orientação das partes
im
p r .

A frente da nossa impressora vai ser o lado onde, na figura, se encontra a mão amarela.

Passo 7


Introduza um parafuso M5
10mm juntamente com um 10mm juntamente com um
teenut em cada um dos carris de z. em seguida introduza um perfil de aluminium de um carri de z para o outro ( é importante de

z para

o outro ( é importante
que esses dois perfiz fiquem nas laterais da máquina).

Em seguida introduza 3 tee nuts Em seguida introduza

3 tee nuts
em cada um dos perfis bem. em cada um desses tee nuts
introduza um parafuso a fim de fixar um angulo de aluminium fixar um angulo de aluminium como se apresenta na figura.

Passo 8


sobre os dois perfis
colocados previamente no
carril de z coloque 3 perfis carril de

z, coloque

3 perfis
de aluminium que vão ser
fixados na parte de baixo
dos “ângulos” de aluminium previamente colocados previamente colocados.

É importante que estes
perfis fiquem mais ou menos equidistantes.

Em seguida coloque 3 tee
nuts por perfil e uma peças quandradas como se quandradas como se
apresenta na figura ao lado fixada em cada tee nut.

Mais uma vez é importante

Passo 9

Mais uma vez

é importante
que as peças fiquem mais o menos equidistantes.

Introduza duas porcas M5 ( uma em cima outra em baixo) em em cima outra em baixo) em cada uma
das peças quadradas
previamente fixadas nos prefis.

Em seguida rosque uma
manipulo de reguração de altura em cada uma das estruturas previamente montadas (peça previamente montadas (peça quadrada fixada no perfil e com duas porcas M5).

Em seguida no topo de cada Em seguida no topo de cada varão coloque um pé

Coloque um perfil em U na
horizontal sobre os “pés” sendo

Passo 10

horizontal sobre os pés sendo que cada perfil vais estar sobre 3 desse pès.


Introduza o carri de X num perfil de aluminium e em seguida coloque em cada extremidade do perfil uma cada extremidade do perfil uma carruagem de Y como na figura.

É importante respeitar a disposição dos carris dos carris.

no caso de ter os carris pré montado retire dos carris de Y as duas rodas que ficam orientadas par fora a fim que ficam orientadas par fora, a fim de introduzir a estrutura na
montagem já efectuada.

Passo 11


Instale os 4 motores de Z nas peças im
p ressas como de acordo com a fi

gura bem
como os acopladores.

Em seguida coloque uma porca M8 em cada um dos carris de Z.

Em seguida rosque o varão de cima para baixo passando pela porca e fixando no aco
plador.

para trancar o varão coloque duas porcas no topo do varão e aperte uma contra a outra.

Passo 12

Introduza os motores ( X Y ) na peças impressas que se encontram nos cantos superiores da montagem bem como um pulley em cada motor.

Passo 13

Olhando de frente para a máquina, introduza a monta
gem do fim de curso, no carril de z de acordo com a figura.

Passo 14

Olhando de frente

p ara a má

quina.

No perfil de aluminium superior introduza 4 Tee Nuts e no perfil inferior 1 Tee Nut.

Instale a montagem do fixador do guida de cabos, no centro do perfil de aluminium superior. Logo ao lado direito instale a monta
gem do extrusor de
acordo com a figura.


Em seguida fixe o perfil que vai guiar os cabos no
perfil inferior.

É importânte respeitar sempre a orientação das montagen em relação á ima
gem.

Passo 15


Neste passo é muito importante fazer o corte do cabo de aço de forma a que não fique desfiado pois isso felicitará os seguintes passos.

Corte o cabo de aço em 8 partes iguais, de comprimento igual a diagonal da máquina.

Em cada um dos cantos impressos tem 2 parafuso fixos por uma porca. Desaperte todos os parafusos de forma a ficarem o mais para fora possivel mas fixos á porca.

Passo 16


Introduza uma peça de fixação na extremidade de um cabo de a
ç o e uma anilha, a

perte os 2

parafusos.

Em seguida passe o cabo por um dos parafusos que encontra já instalado num dos cantos impressos e passe também pelo p arafusos do canto o

posto ficando o cabo na dia

gonal.

Introduza uma anilha na ponta do cabo de aço e de seguida uma peça de fixação, estique o cabo e com o cabo em tensão a
p erte os 2

parafusos do fixador.

repita Estes passos para as outras 7 diagonais da máquina. Por fim aperte os parafusos por onde o cabo passou até estarem em tesão.

Passo 17


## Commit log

2016-04-04 added STEP assembly
2016-04-04 update assembly guide
